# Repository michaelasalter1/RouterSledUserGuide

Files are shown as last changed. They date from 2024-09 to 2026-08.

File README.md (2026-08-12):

# RouterSledUserGuide
I built a Router Sled to flatten wood slabs and make Epoxy River Tables. This is to share how I did it and provide some helpful lessons I learned along the way.

## Router Sled Parts
- Hoist Gantry – Used to flip large slabs with the help of snatch rings, winches, and rope.
- Router Gantry – Holds the router
- Riser Rails – Added to provide more clearance when surfacing extra tall work pieces. The riser rails and the posts have coinciding numbers for ease of install. You will need to level these to ensure they are as flat as possible.
- Foundation – Holds everything together. The foot of post #2 (the one closest to the door) has shims underneath it. While there are leveling feet in each post, I found shims easier. I have also marked the floor with gold spray paint for reference since concrete is not always perfectly flat. I did add reinforcement strips near the floor between each post. They make sweeping a pain but reinforce the foot location to help prevent racking. Racking could cause coplanar issues when flattening big pieces.
- Rails – **DO NOT DAMAGE THESE!**
  - While the rails are part of the foundation, they are the most important part on this entire structure. The Router Gantry uses these for reference. Every effort has been made to ensure these are perfectly flat, level, and coplanar. The pine rails tend to splinter the tops and inner sides with repeated use. This is not surprising since this is where the bearings on the router gantry contact the rails. To prevent this, I coated these sections of the rails with epoxy and sanded them flat to enhance their durability.
  - When lowering your router height, do so with the router near the edge of the rails closes to you, as this will minimizing creating sagging in the gantry rails.
  - When you intend to mill wide slabs, or you need the best results possible, it is a good idea to check the levelness of the gantry rails periodically to ensure they have not started to sag from mishandling.
    - Use a 4’ Level from Harbor Freight to check.
    - If the gantry rails are not level, place (2) stacked 2x4s or a 4x4 in the middle of the foundation and add a clamp to each side of ONE gantry rail and straighten each rail separately. Only aim to create ~1/2” bend in the rail at a time to slowly reshape it.  
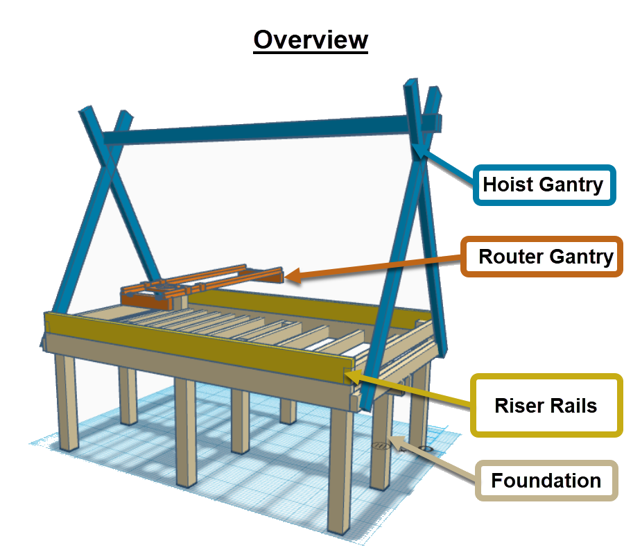
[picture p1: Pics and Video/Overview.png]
Router Sled Overview
  
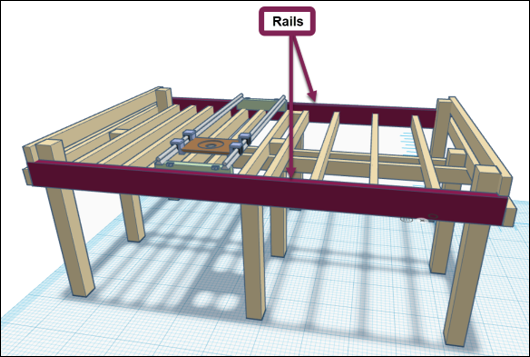
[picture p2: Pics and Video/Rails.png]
Router Sled Rails
  

## Router Gantry
- Bearing Assembly (4) – guides router gantry along rails
- Gantry Tensioner (3) – (not pictured) but mounted between the bearing assemblies on either end of the router gantry to help keep the gantry from racking.
- Bearing Housing Offset (2 Left, 2 Right) – serves as a mount between the linear bearings and the router base. Decreases clearance of the router to the workpiece.  
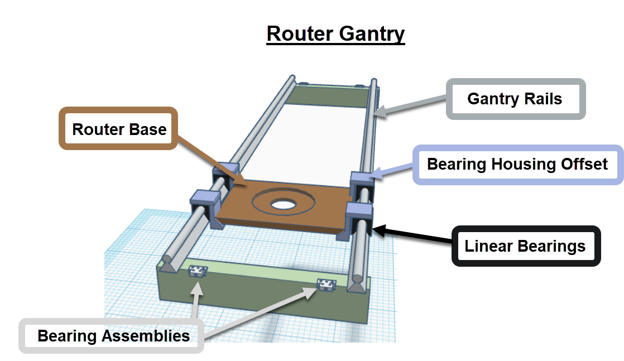
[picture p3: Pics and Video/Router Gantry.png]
Router Gantry


## Bearing Assembly
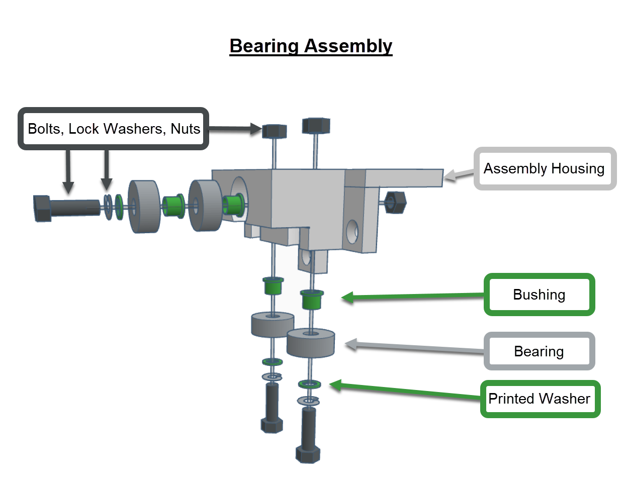
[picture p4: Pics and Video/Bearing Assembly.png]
Bearing Assembly


## Accessories
Accessories
- Plunge Router Depth Stop increment gauges  
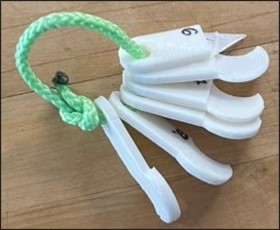
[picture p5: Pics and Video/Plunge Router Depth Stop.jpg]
Plunge Router Depth Stop Increment Gauges


- Dust Separator with pressure relief valve. I’m using a 5 hp ridgid shop vac.  
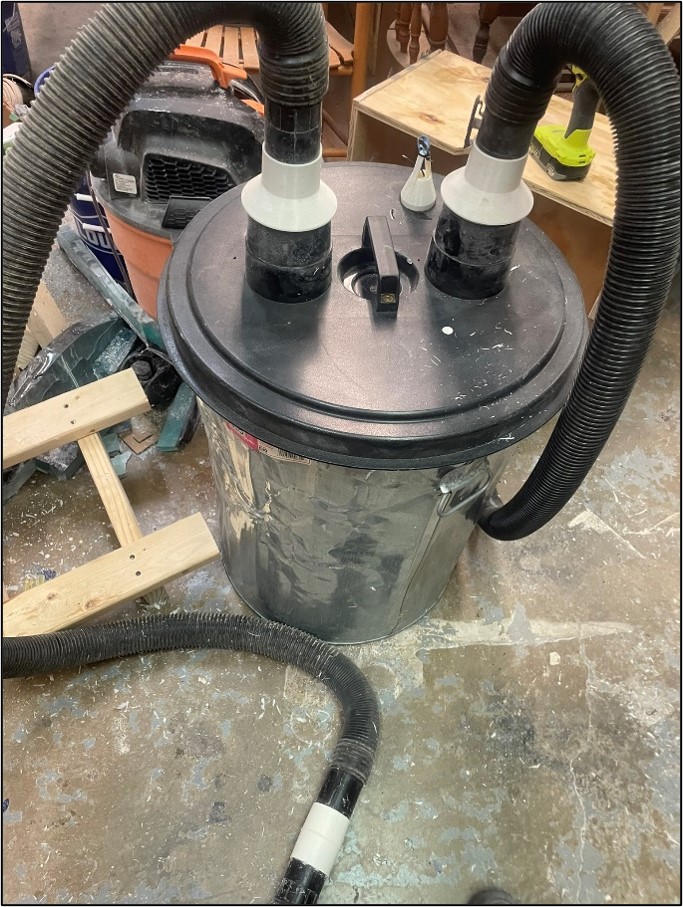
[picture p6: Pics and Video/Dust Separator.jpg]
Dust Separator


Without the relief valve, the trash can collapses, and the suction becomes worthless.  
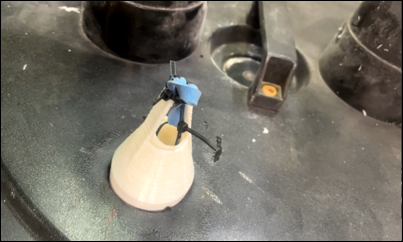
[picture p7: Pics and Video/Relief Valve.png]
Pressure Relief Valve


## Part Replacement
All parts were printed with Hatchbox’s 1.75 PETG filament with 5 shells and 35% infill for maximum rigidity and durability. The settings captured below are mostly for my reference.

I printed on a FlashForge Creator Pro using the following settings. I preheated the build plate and kept the chamber closed to maintain a steady temperature. If you do not do this, the bearing assemblies will warp.
Cura print settings for bushings and washers: infill didn’t matter, no support, no raft, 

Flashprint is great for supports. However, I had problems with it printing the bushings and washers; they didn’t want to adhere to the bed. So, I used Cura to print those. Therefore, you will need to calibrate the holes for the bushings and housings AND for the bearing assemblies (they are different).
Test Print Calibration – Use these 2 files to dial in the calibration of holes before printing the assemblies.

All Printed Parts Used for this build:
- (4) Bearing Assemblies
- (16) bushings (4 per assembly, printed in Cura)
- (12) printed washers (3 per assembly, printed in Cura)
- (2) Left Bearing Housing Offsets
- (2) Right Bearing Housing Offsets
- 2.5” Vacuum Hose Coupler
- (2) 4” to 2.5” Hose Adapter
- Pressure relief valve (eloquently calibrated via zip ties and broccoli rubber band)

## Purchased Hardware
### Foundation, Rails, Riser Rails, and Hoist Gantry
- Lumber
  - 2 x 4 x 8
  - 2 x 4 x 10
  - 2 x 6 x 10
  - 4 x 4
- ½” Nuts
- ½” Bolts
  - 6” 
  - 8”
- (9) Adjustable Feet
- (2) Cable Puller (Harbor Freight)
- (2) Snatch Ring (Amazon)
- Rope (Amazon)

### Router Gantry
- Router Base bolts
- Bearing Housing Offset bolts
- Rails
- Linear Bearings

### Bearing Assemblies
- Horizontal bolts are ¼” x 1.5”
- Vertical bolts are ¼” x 2”
- Split Lock Washers ¼”

# Flattening
Materials
- Router
- Bit
- (2) Bit Extension - one for flexibility, second is for leveling the foundation (Spoilboard)

## Directions
Route/flatten towards you and to the left in ~1” passes has worked the best for me. Some prefer to run it with the grain. If milling epoxy, here are a few tips that help:
1. Warm the epoxy before the pass with a heat gun 
2. Turning off the AC in the room for a few days
3. Use fresh blades on your router bit
4. Taking really small passes with the router (like ¾” max and slow)
5. Chipout can be repaired with CA glue.
6. If you create a crack in the epoxy, sand it down with angle grinder or aggressive sander, and pour a patch of color-matched epoxy

## Oversize Pieces
For workpieces that are greater than the two furthest cross members, you may slide the piece down to flatten one end, then slide it the other way to flatten the other. Doing so, will not be perfect, but is a serviceable solution provided the workpiece is not too tall to slide below the frame.

## Reflatten the Foundation
If you need it perfectly flat, use a second bit extension to flatten the foundation. I have spary painted spots on the floor for where I leveled the foundation to. The leg closes to the door (leg 2, as denoted on the top of the post) has a shim under it.

# Rig, Hoist, Flip
## Overview
**_WARNING:_** This Router Sled and all accessories belong to the River Park Wood and Art Club. This is not a professional setup. By using this, you accept the risk and liability. Before using this, you must be a member of the River Park Wood and Art Club, and therefore have signed the liability release waiver.  

**_WARNING:_** Never lift overhead and never get under a workpiece. Always add backup safety straps whenever lifting in case of main rope failure.  

This guide is meant to serve as a starting basis on how to rig, hoist, and flip a workpiece with limited risk. 
- Working Load Limit (WLL) is a fraction of the Breaking Strength (BS). For this system, due to the limited hoist length, and non-overhead use. 
- For ratings in kN, 1 kN is ~220 lbs, so a 23 kN limit = 5060 lbs.

## Rope
The weakest point in a rope is the knot. Most knots diminish the WLL by 25-50%; some up to 75%. So, a working load of 1000 lbs. could become as little as 250 lbs. 
The [Orange rope in the Old Art Room](https://www.amazon.com/gp/product/B093PQQ375/ref=ppx_yo_dt_b_search_asin_title?ie=UTF8&psc=1):
- WLL of 528 lbs. BS of 3520 lbs. With a figure 8 knot, the BS is 2,650 lbs and has a WLL of 528 lbs when using a safety factor of 5.
- Rope due for disposal on June 28, 2034. (10 years from date of purchase)

## Rig
When rigging a slab or completed piece to hoist, the angle of the sling around your workpiece further increases the tension on the rope.

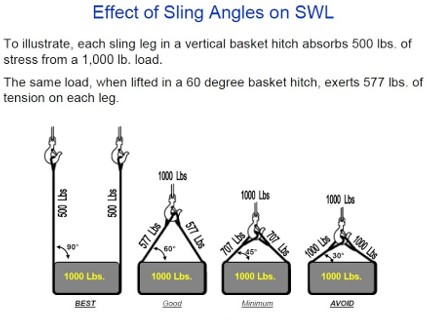
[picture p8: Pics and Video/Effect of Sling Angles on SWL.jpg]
Effect of Sling Angles on SWL


As demonstrated in the image above, as the sling length decreases, the angle of the sling legs decreases, which multiplies the load added to the rope. 

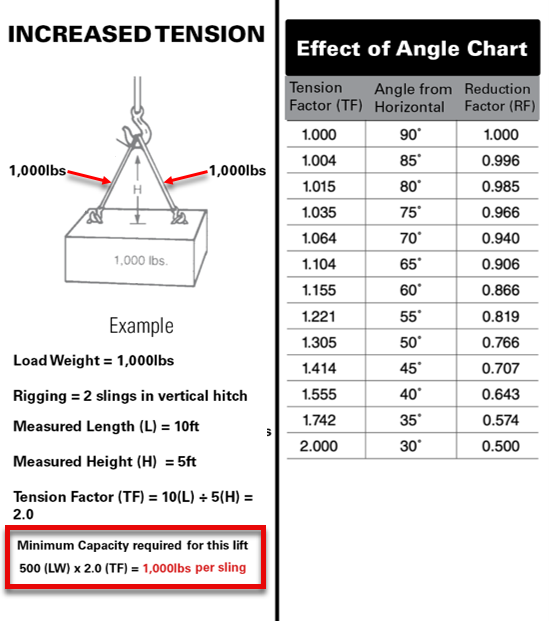
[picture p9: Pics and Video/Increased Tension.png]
Increased Tension


For 60-degree sling angles, the WLL of the supplied rope decreases from 528 lbs down to 457 lbs.
For quick reference, the table below is 7’1” x 46” x 1/75” and weighs roughly 300 lbs. Each walnut slab is 70-80 lbs, and the uncured epoxy weight is 126 lbs (14 gallons).

## Hoist
Avoid jerking the load as you hoist it up or down. Jerky maneuvering can easily double the load weight.

## Flip
[How to Flip a Load](https://www.youtube.com/watch?v=W16BWTuQFtc)

# Table Legs
There is not good guidance on the width of table legs. However, if you are doing a river table, you don’t want to drill into epoxy; the hardware will show through, and it can also crack. 

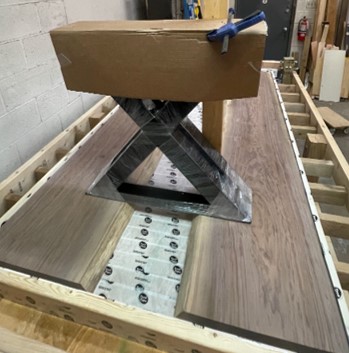
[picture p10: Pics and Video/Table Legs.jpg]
Table Leg Problem
  
For this table, I could only use a tiny portion of the bolt holes, which wasn’t ideal for a table of 300 lbs.

So, I cut off the crossmember, had 6”x 6” plates welded to each side, drilled holes, and painted. Avoid the added cost and work. For a table like this, the holes should be at least 4” apart. If you are doing etsy, spend an extra $50-100 to have extra plate welded if you think it suits your use case. For reference, these table legs were $400 before the extra $200 to have the plates welded. Seems like a lot, but that’s comparatively cheap; table legs are expensive. 

Fwiw, Hammered black satin by Rust-oleum is a decent match, but certainly not perfect.  
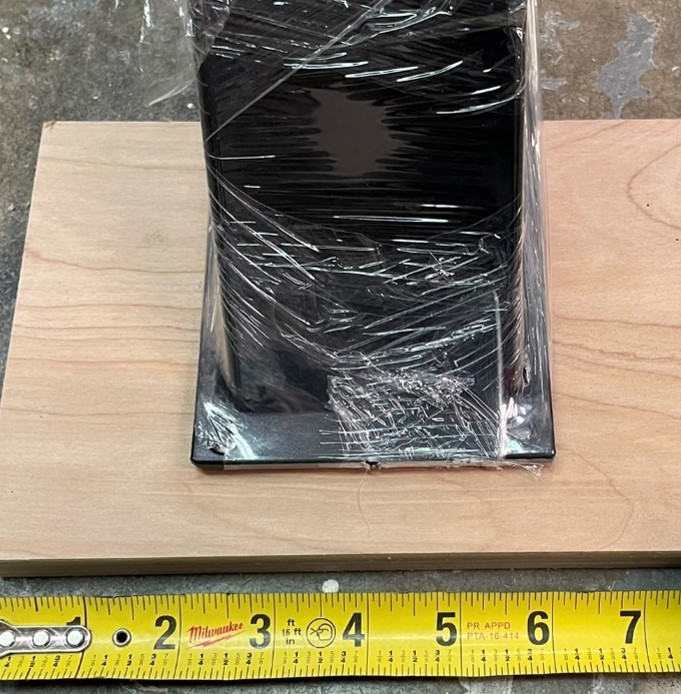
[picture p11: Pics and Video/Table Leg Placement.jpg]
Table Leg Placement


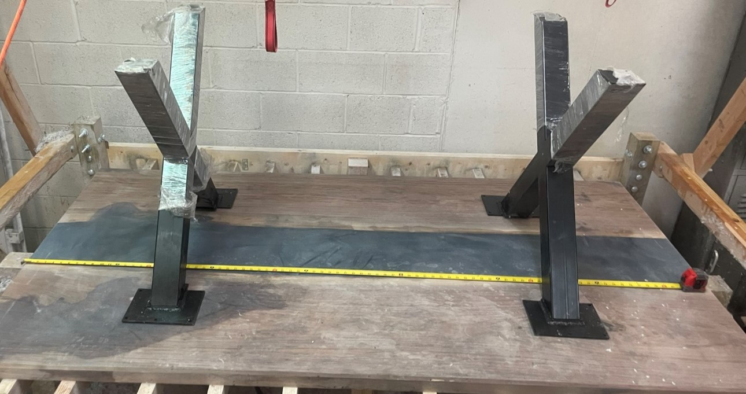
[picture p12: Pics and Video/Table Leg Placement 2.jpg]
Table Leg Placement 2
  

# Epoxy!
Making an epoxy table requires a lot of tools and materials. I’ve created a list with notes here: [Amazon Tools and Materials List].(https://www.amazon.com/hz/wishlist/ls/2T5CPWIJCLLNZ/ref=nav_wishlist_lists_2)
I used Blacktail studio’s Epoxy table workshop course. The following sections identify things I’ve learned that work well for me.

## Calculating Epoxy
The bottom of your pour will not be a solid layer of epoxy, even if your slabs are perfectly flat. The bottom will most likely need to be flattened when you finish because not only will you get weird pockets of epoxy and non-epoxy, every tuck tape seam will show.

Calculating the bottom layer is difficult, and you never get an even layer. Here is some overage since I only wanted a 1/4” in order to have a dark bottom layer.  
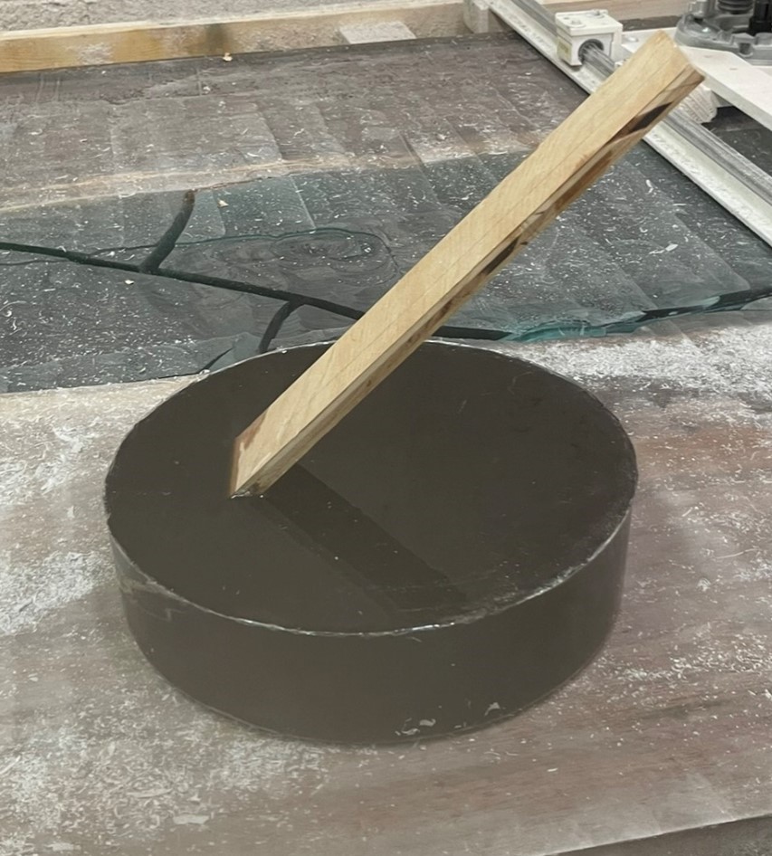
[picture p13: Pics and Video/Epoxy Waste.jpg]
Epoxy Waste


## Sealing
- If the Old Art Room has the AC running, a sealer coat takes 16 hours, otherwise 18-20 hours.
- Any cracks in wood can easily leave bubble trails. Fully seal before you pour either with epoxy or with Thick CA glue. 
- I did walnut. Some sections, especially a ledge, took 6 coats to fully seal. After 2 coats, use a tabletop epoxy if you are on a timeline.
  - Sand with 180 between sealer coats
  - Sanded epoxy creates a white powder. If there is a bubble that is filled with epoxy powder, on the next sealer coat, dab at it with your brush to make it clear again. Alternatively, you can blow it out, vacuum it out, or use dental picks or screws. These bubbles tend to be big enough where the brush works just fine though.
- If you plan on sealing your workpiece propped above your form, and are not immediately going to drop the piece into the form (like if the workpiece might need more than one sealer coat)
  - Cover your form with a plastic drop cloth. Otherwise, drips will screw up your form and your form will have to be reprepped before the pour.
  - For the sealer coat, allow your workpiece to dry with the topside down (that is the last side to be fully submerged during the pour facing down). Otherwise, the sealer coat drip marks are more important to deal with, and that’s a waste of time. To elaborate, how they are drying here, if I didn’t sand the drip marks off, it would throw off the width of my table.  
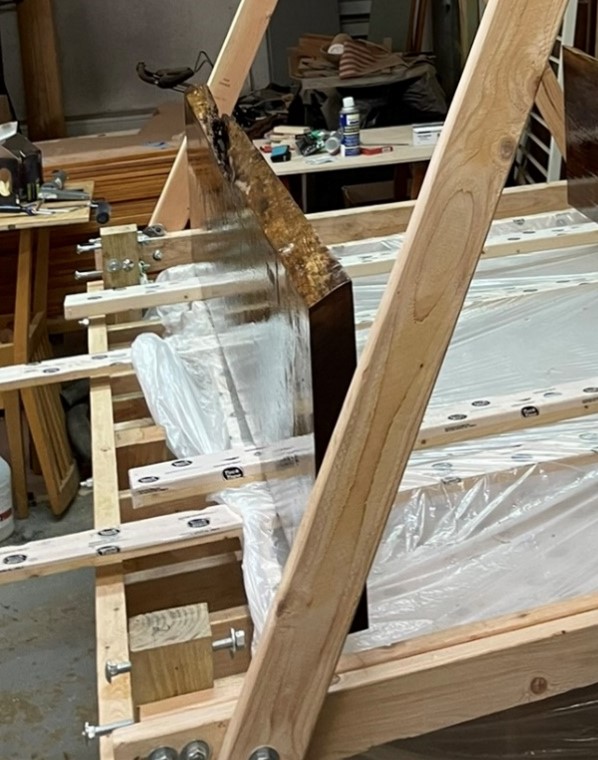
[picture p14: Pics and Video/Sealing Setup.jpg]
Sealing Setup


## Caulk
I used GE Window & Door Projects All Purpose Silicone, and it worked perfectly. Keep in mind that the seam will cause your slab not to seat perfectly on the edges. For my 4’ wide table, I lost 1/4” width.  
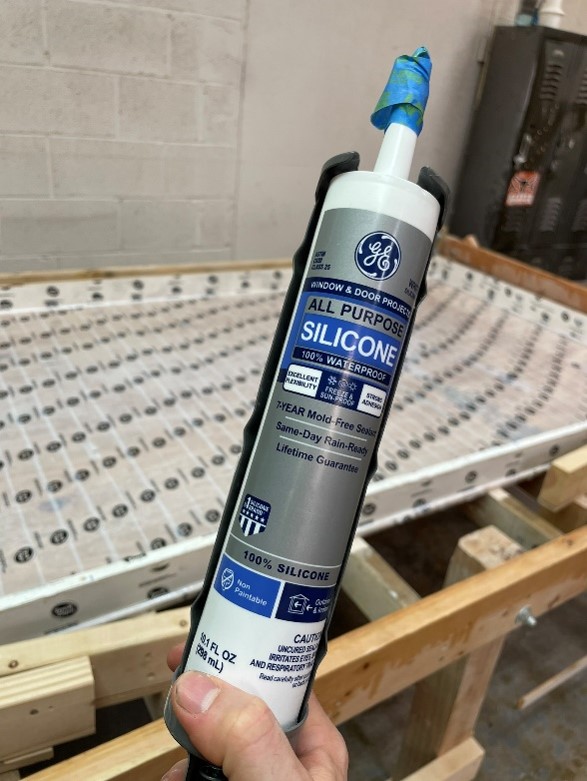
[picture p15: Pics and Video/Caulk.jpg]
GE All Purpose Silicone


## Prepour
-	Wipe down with isopropyl 91+. Safeway has cheap bottles, but the ones from harris teeter have the squirt top.
-	Cool the room and use fans above and below the foundation to keep it cool. 
  - I know without AC you can get away with ~2 gallons at 80 degrees in the Old Art Room. 
  - For big pours (greater than 6 gallons), cool the epoxy (keep it in the old art room) for a few days prior to pour to keep it from overheating and cracking.
    - With AC on full blast and a few days to cool off, I did a 6 gallon pour successfully. You can probably get away with more, but I figured better safe than sorry.

## Pour
- If the Old Art Room has the AC running, 3-6 gallons takes ~39 hours to cure depending on humidity (for pours 0.25” to 1.25”).
- If you really are looking for a perfect pour, don’t. But you can try degassing the epoxy, and plan on possibly not using a fan above the pour. The fan may or may not have caused more bubbles in my last pour. It’s voodoo at this point for me.

## Between Coats for Multi-Pour
- I found that sanding to 180 grit is rough enough for epoxy to bond to itself and not leave residue. In fact, when my project failed, the two pour layers adhered well enough to one aonther that it actually broke the bottom layer that had already previously cured.
- If 2-part pour, and there are pits on the bottom layer from bubbles, watch out for sanding dust. If so, either clean out with vacuum/air, pick with dental pics, or force epoxy into it with a brush on next pour. I’d recommend pouring isopropyl on it to determine what needs to be addressed before doing the next pour
- If clear/translucent, make sure there are no fingerprints.
- Wipe with isopropyl 70+. Dries quicker than water.

## Fail
If the pour gets too hot, the epoxy will cure too fast and then crack. 
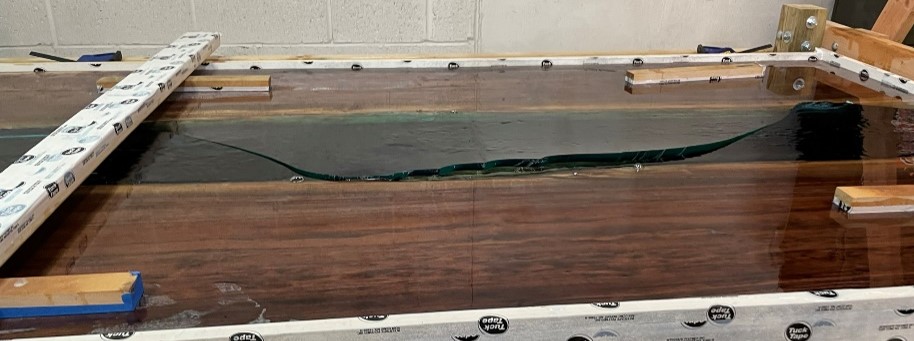
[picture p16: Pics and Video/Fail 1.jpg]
Fail 1

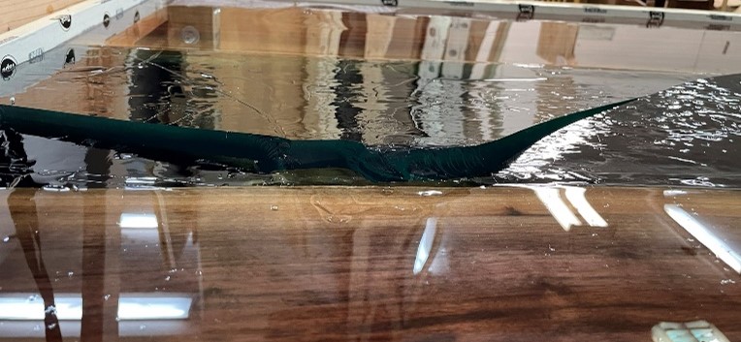
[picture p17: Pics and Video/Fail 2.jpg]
Fail 2

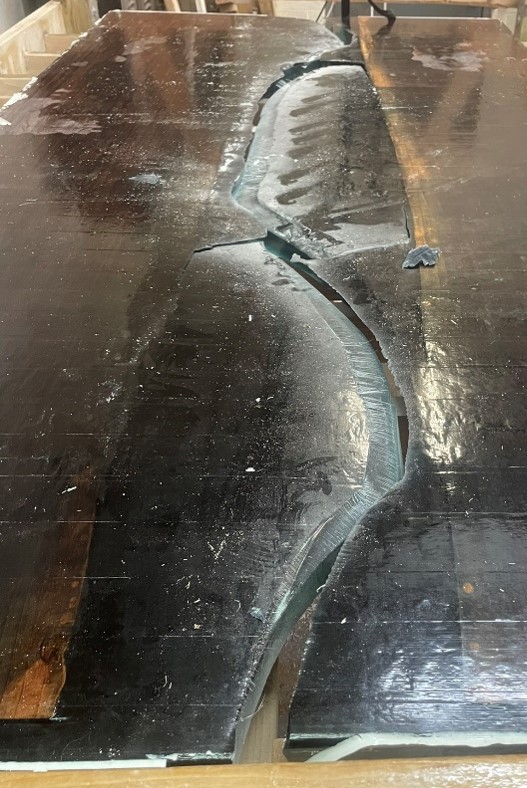
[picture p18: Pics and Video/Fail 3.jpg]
Fail 3


You can throw it away or spend $100 on a 4.5” angle grinder and accessories from Harbor Freight. It’s actually lots of fun. But super messy. Use a respirator and goggles. Swim goggles are great for this task.  
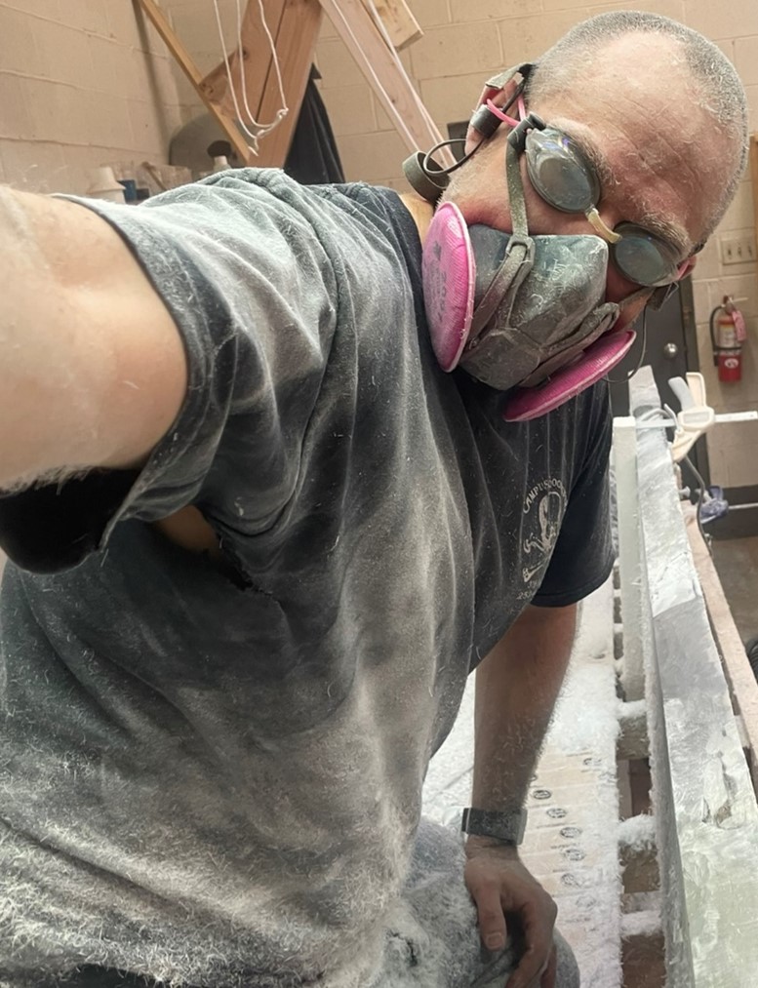
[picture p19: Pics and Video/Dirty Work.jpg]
Messy


- To repair cracked epoxy: Circular saw > Jigsaw (optional) > Angle Grinder (AG) with Segmented Wheel > AG Steel Wood-Shaping Dish > AG 36 grit sanding disc > Sander. 
- If color matching is a thing and you are concerned about transition colors, accept the fact that you will reshape when you gouge the wood if dealing with intricate stuff.
  - As I'm writing this, I'm actually wondering if that was overkill and it would have blended well without me going all the way back to bare wood.  
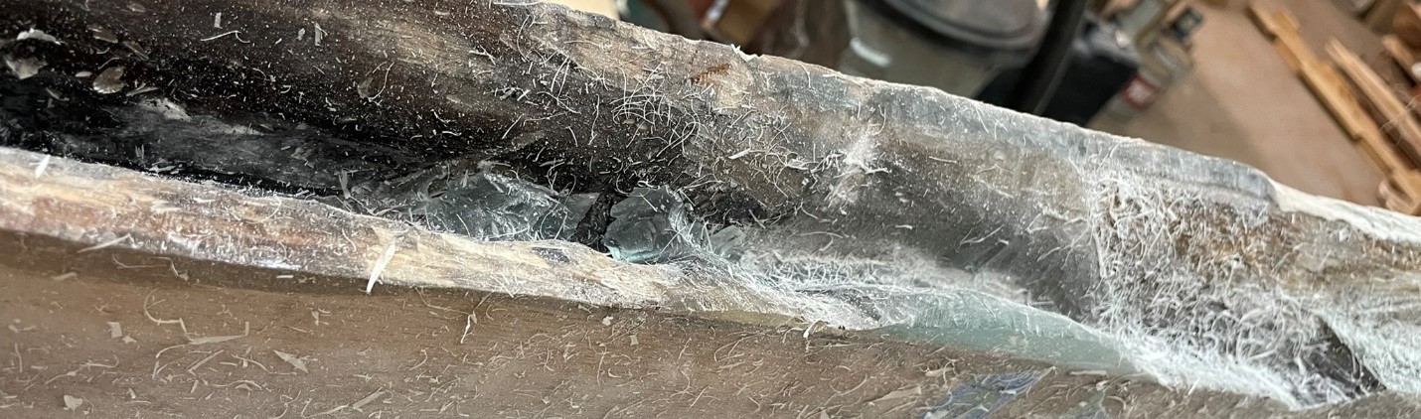
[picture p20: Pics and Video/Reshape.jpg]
Reshape


- For intricate stuff or weird shapes around the live edge, a Dremel with bur bits and then upcut or downcut bits work well.  
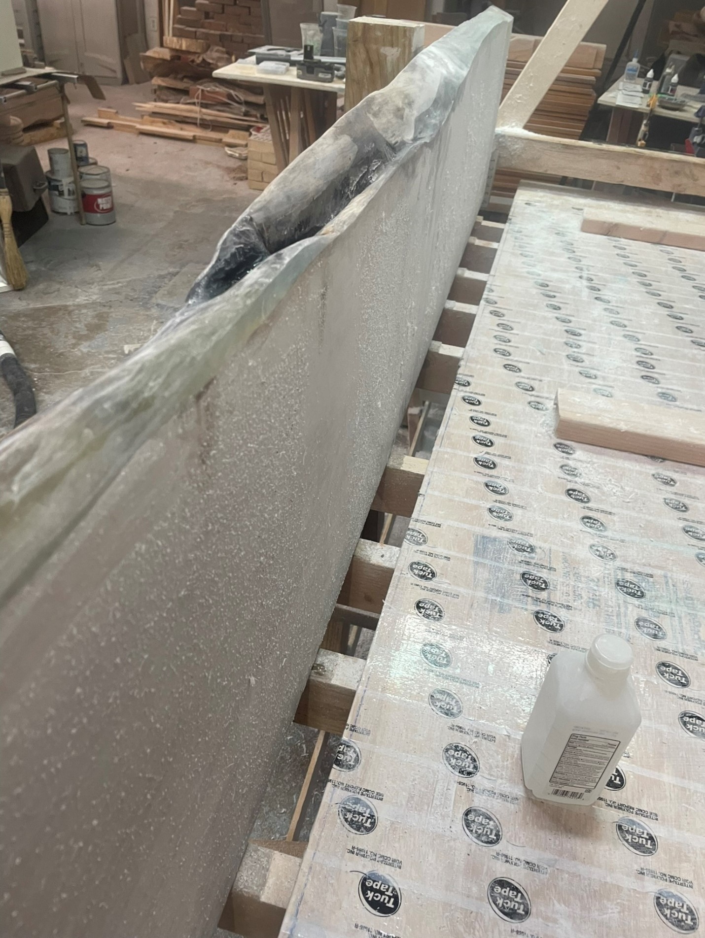
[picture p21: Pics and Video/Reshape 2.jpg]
Reshape 2


# Finishing
## Repair Imperfection
Use clear CA glue unless the hole is big enough to not drip black outside of it. Otherwise, it will bleed.  
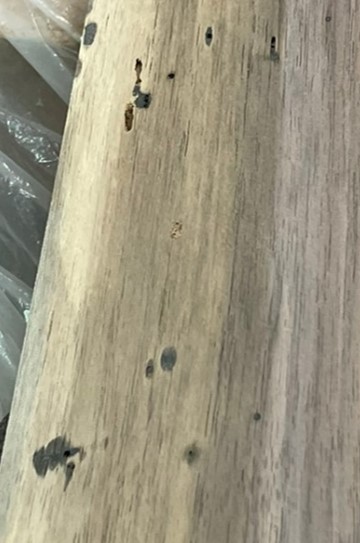
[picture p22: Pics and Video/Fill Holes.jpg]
Epoxy Fill Holes


Accelerator is good when the crack is big enough to need thick epoxy. Otherwise, the accelerator can cause the glue to turn white or can leave a gap below the top layer that you will struggle to fill as you progressively sand finer.  

Here’s what the progression looks like: CA, sand 180, CA, sand 120, CA, sand 180, CA, sand 180, give up. If you have holes, eventually the table will reveal more with use. That's part of working with a natural product.  
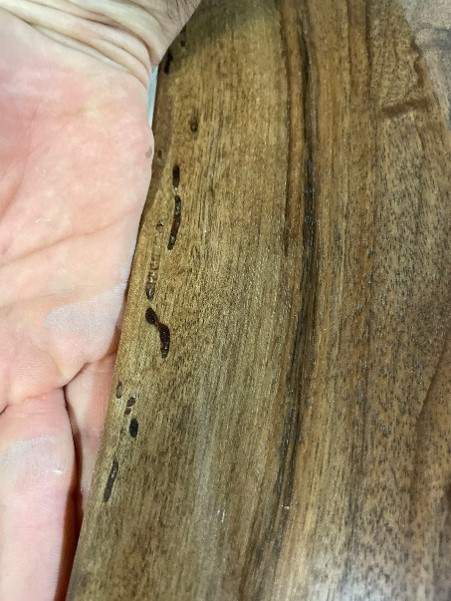
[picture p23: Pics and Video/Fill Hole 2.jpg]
Epoxy Fill Holes 2


## Sander
A great sander will save you hours. I originally bought this Bosch 5” Random Orbital Sander thinking it would be phenomenal. For big projects, or small epoxy projects, you will spend hours sanding. I only use this if I am going to polish something now.

By “great” sander, I mean one with a stroke length (also called Orbit Diameter) of at least 3mm; but 5mm is ideal. You also need active dust collection for your sandpaper to last.

I did my research and at the time (2023) the only two quality brands on the market are Festool and Mirka. I didn’t like the paddle switch on the Mirka because I like to change my grip and was ultimately between the Festool RO150 (6” Rotex) and the Festool ETS EC 150/5. I went with the 150/5 because the I wanted a more ergonomic sander, thought the Rotex mode wasn’t something I would need too often, and ultimately didn’t want to spend any more. You also need protection pads (non-cushioned interface pads), Interface pads (buy the thin one that’s a 2 pack), and the two separate dustright connectors for a shopvac while you are there: Dust Right Click-Connect FlexiPort (I don’t know which size) & Adapter.
To see how much a good sander makes a difference: 

Sanding

- I use 3M Cubitron (80, 120, and 180 grit) sandpaper. On wood, it lasts way longer than any other sandpaper, so ultimately it is cheaper. Check TayTools, Amazon, and Rockler for sales. Woodcraft doesn’t carry it. Use a non-cushioned interface pad (like I recommended above) when using this sandpaper. Cheaper to replace these than the sander baseplate.
- If you get swirl marks (pig tails), your sandpaper is clogged. Replace it with the same grit and sand until the swirl is gone. You cannot sand past the swirls with a finer grit.
- Spray wood with isopropyl 70 proof between grits (water pop) and allow a little time to dry. It will raise the grain and give you better results.

# Appendix
## Calculations
- [FGCI Deep Pour 2-4” Epoxy](https://www.superepoxysystems.com/product/liquid-glass-deep-pour-epoxy/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) uncured weight: 9 lbs/gallon.
- [FGCI](https://www.google.com/url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)
- [Blacktail] (https://www.blacktailstudio.com/epoxycalculator)

# Rigging Knots
- Alpine Butterfly
- Bowline
- Constrictor knot – Cannot be untied!
- Figure 8
- [Retraced Figure 8](https://www.alpinesavvy.com/blog/how-to-tie-the-perfect-retraced-figure-8)

 ## Common Lumber Weight and Hardness
(Common Wood Species Guide](https://www.wood-database.com/)  
Species/Average Dried Weight (lbs/ft^3)/Janka Harness (Newtons)  
-Cedar
  - Eastern Aromatic (Red) Cedar -- 4000
  - Western (White) Cedar
- Maple
  - Hard Maple 44	6450
  - Silver Maple 33	3110
  - Soft Maple  
- Oak
  - Red Oak 44	5430
  - White Oak
- Pine 28-34	2050-2250
- Poplar 2400
- Rubberwood
- Walnut
  - Black Walnut	38	4490
  - English Walnut

## Source Print Models
- [The original router sled design](https://www.thingiverse.com/thing:4565094)
- [Remix of Router Sled Handle](https://www.thingiverse.com/thing:5330170)
- [Adapter 4" to 2.5" dust collector](https://www.printables.com/en/model/589597-shop-vac-tool-adapter-4-to-2-15-hose)
- [Craftsman Shopvac Replacement Foot](https://www.thingiverse.com/thing:5909428)
- [Dust Collection Relief Valve](https://www.thingiverse.com/thing:3644937)

## Amazon Purchase Lists
- [Router Sled Materials](https://www.amazon.com/hz/wishlist/ls/3G5MYD8QBKA7V?ref_=wl_share)
- [Amazon List of Epoxy Supplies](https://www.amazon.com/hz/wishlist/ls/2T5CPWIJCLLNZ?ref_=wl_share)

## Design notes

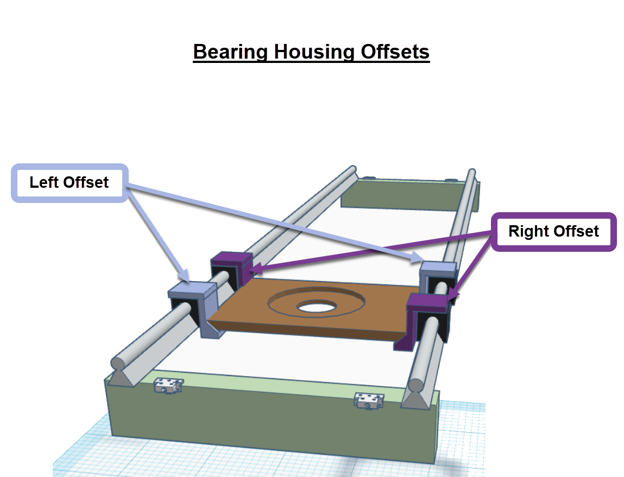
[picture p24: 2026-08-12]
Pics and Video/Bearing Housing Offsets.png

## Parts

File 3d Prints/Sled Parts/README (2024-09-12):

I have a FlashForge Creator Pro. I calibrated some, then just changed the print dimensions at a certain point. The Bushing and Washer did not print well in FlashPrint, but did fine in Cura.

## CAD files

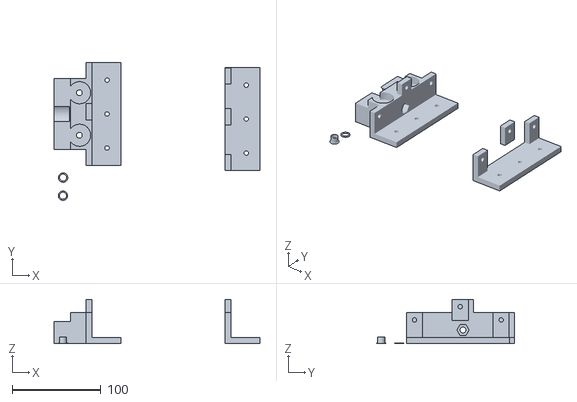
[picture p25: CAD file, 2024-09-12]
3d Prints/Sled Parts/Bearing Assembly and Bushings.stl
232.5 x 155.5 x 49.9

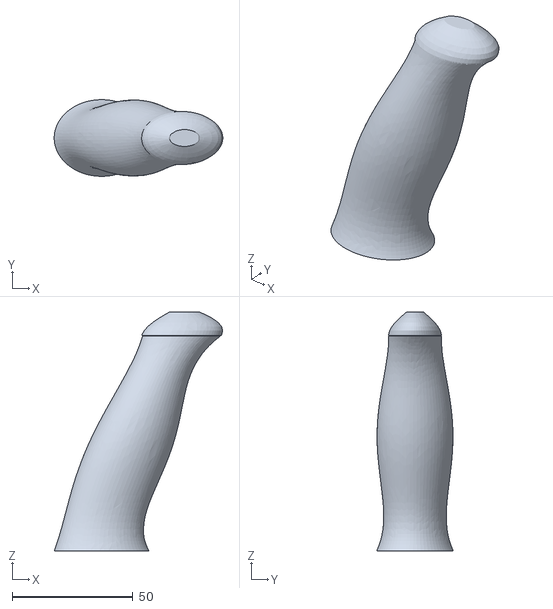
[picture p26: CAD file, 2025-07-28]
3d Prints/Sled Parts/Router Sled Handle.stl
69.7 x 31.7 x 98.8

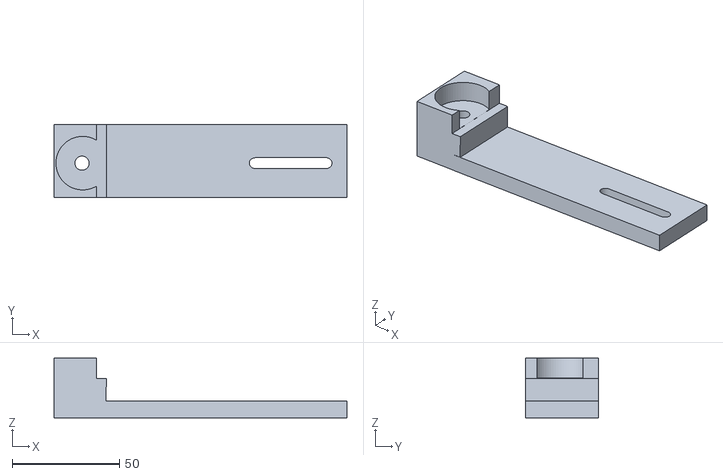
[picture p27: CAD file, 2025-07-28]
3d Prints/Sled Parts/Gantry tensioner-2.stl
136.8 x 34.2 x 28.0

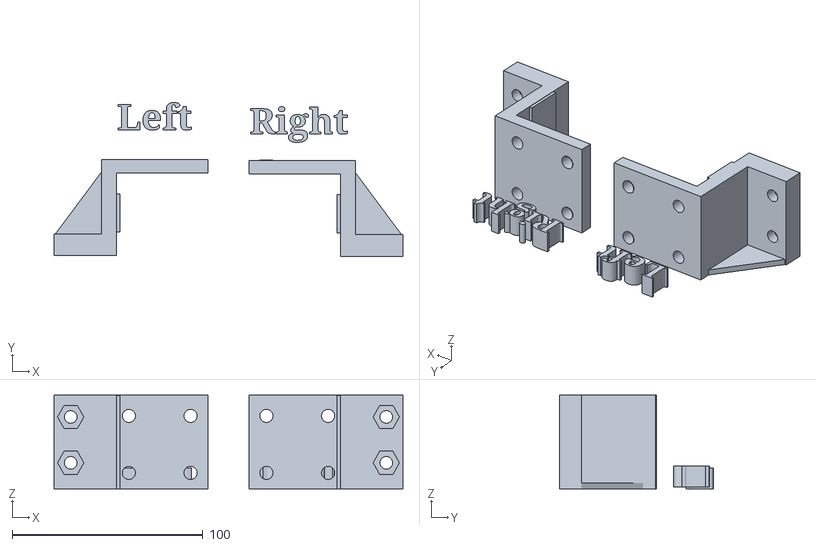
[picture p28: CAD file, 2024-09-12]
3d Prints/Sled Parts/Router Platform Offset.stl
182.8 x 80.5 x 49.0

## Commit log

2024-09-11 3d Printed- Router Sled Safe
2024-09-11 Router Sled Handle, manual pause 41 mins for nut
2024-09-11 3d Parts
    [4 to 2.5 vacuum Dust Collection.stl]
2024-09-12 Update and rename Router Sled Handle 41.x3g to 3d Prints/Router Sled Handle 41.x3g
2024-09-12 Rename 3d Prints/Bearing Assembly v3 .05.x3g to 3d Prints/Sled Parts/Bearing Assembly v3 .05.x3g
2024-09-12 Rename 3d Prints/Bearing Offset Left.fpp to 3d Prints/Sled Parts/Bearing Offset Left.fpp
2024-09-12 Rename 3d Prints/Bearing Offset Left.x3g to 3d Prints/Sled Parts/Bearing Offset Left.x3g
2024-09-12 Rename 3d Prints/Bearing Offset Right.fpp to 3d Prints/Sled Parts/Bearing Offset Right.fpp
2024-09-12 Rename 3d Prints/Bearing Offset Right.x3g to 3d Prints/Sled Parts/Bearing Offset Right.x3g
2024-09-12 Rename 3d Prints/CPRO_Bushing .03 offset.x3g to 3d Prints/Sled Parts/CPRO_Bushing .03 offset.x3g
2024-09-12 Rename 3d Prints/CPRO_Washer .03.x3g to 3d Prints/Sled Parts/CPRO_Washer .03.x3g
2024-09-12 Rename 3d Prints/Gantry tensioner-2.x3g to 3d Prints/Sled Parts/Gantry tensioner-2.x3g
2024-09-12 Update and rename 3d Prints/Router Sled Handle 41.x3g to 3d Prints/Sled Parts/Router Sled Handle 41.x3g
2024-09-12 Rename 3d Prints/Router Platform Offset.stl to 3d Prints/Sled Parts/Router Platform Offset.stl
    [Router Platform Offset.stl]
2024-09-12 Update and rename Bearing Assembly v3 .05.x3g to Bearing Assembly v3.x3g
